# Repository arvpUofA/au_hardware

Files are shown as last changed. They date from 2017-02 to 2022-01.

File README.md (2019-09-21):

# au_hardware #

Welcome to ARVP's hardware design repository.

In here you can find all of our electrical designs.

### Github Guides
- http://rogerdudler.github.io/git-guide/ 
- Intro to GitHub with Hello World
- https://www.youtube.com/watch?v=0fKg7e37bQE 

## Branches
- master -  contains boards that have been fabricated, soldered, tested and are part of this year’s robot
- develop - contains boards that have been designed, approved, and the fab company has accepted their designs.
- project_branch - every new project is branched from develop. Naming convention of branch is as follows:

All names in lowercase and can only include alphanumeric characters and underscores.
The naming format will be `project_board` (e.g. `motor_breakout` or `power_main`)
If the project only contains one board (e.g. `killswitch`) then naming format will be `project`.
If this is a newer iteration of the same board create a branch with the version number `project_board_vx` (where `x` is the version number).

## Starting a new project

```
    # Clone the develop branch of the repository
    git clone -b develop https://github.com/arvpUofA/au_hardware 
    # Create a new branch from develop
    git checkout -b project_board   
    # Push the branch to remote
    git push -u origin project_board
```

Create folder structure for project as follows:
Inside the `au_hardware`/`project_board` branch, create the project folder if it does not exist. (e.g. `motor`, `power`, etc)
Inside the project folder create a board folder if it does not exist. If this is a different version of the same board, don’t create a new folder. Use the same folder as before. If the project contains only one board, you don’t need to create this folder.
Naming of the folder will follow the same conventions as branch naming conventions (no spaces please). 
Add required files to this folder. Make sure to commit and push periodically.

## Project requirements
Once the board design is complete, run the following:

- ERC on schematic - error checking for schematic
- DRC on board - design rule check for pcb. (e.g. drc/JLCPCB2Layer.drc file)
- Generate image files for schematic and pcb. Make sure the images are clear with at least 200dpi.
- Generate CAM files.
- Test CAM files using a CAM Viewer (e.g. View Mate or Gerbv)

Each project needs the following files:
- [ ] project_board.sch - schematic file for project
- [ ] project_board.brd - board file for project
- [ ] project_board_sch.png - image of schematic
- [ ] project_board_brd.png - image of pcb
- [ ] project_board/ - this folder contains all the CAM files
- [ ] project_board.zip - ZIP of the CAM folder

## Pull request and close

Once all requirements have been complete, create a pull request to merge this branch into develop

Set base: `develop` and compare: `your_branch`. Click "Create pull request".
 
Set the PR name, create a detailed description, and assign the team lead to review your pull request.   
The reviewer will check your design, and rerun ERC and DRC.

If the reviewer has any suggestions, implement them in your design, regenerate all required files and commit and push everything.

After the review is complete, the board will be uploaded to the fabrication website. If they approve the design, the reviewer will merge and close the pull request. Make sure you don’t continue work on this closed branch.
A new release tag will also be created for the board with format boardname[version]. E.g. killswitch1.0. At any point you can look at any older version by going to that specific tag.
Note that, if during reviews we discovered any changes we want to make in the next version, we will put these as issues on the repository and assign them to you. These need to be fixed in the next version before you make a PR.

## Starting a new revision

Once your PRs have been closed a.k.a the board has been sent out, the branch you were working on will be deleted, and you will need to make
a new branch off `develop` with the latest version number for that board.

```
    # To start switch to develop
    git checkout develop
    # Pull the latest version of the code
    git pull 
```

Create a new branch for the next iteration of the board. The naming format for the branch is `boardname_vx`

```
    # Example for V2 of comm_hub
    git checkout -b comm_hub_v2
```

Find the appropriate project folder where the current board revision is saved (e.g.  communications_hub) and create a new folder within this project folder with the new version number (e.g. communications_hub\communications_hub_v2).
Make sure to push your new branch to github using 

```
git push -u origin name_of_new_branch
```

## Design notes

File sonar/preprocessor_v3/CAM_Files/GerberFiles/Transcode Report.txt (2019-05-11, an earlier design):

   ---- Transcoding 'C:\Users\Andrew\Documents\Business\ARVP\au_hardware\sonar\preprocessor_v4\CAM_Files\GerberFiles\copper_inner_l2.gbr' ----   Wed Dec 26 16:14:29 2018

D10   --> D100
D12   --> D101
D13   --> D102
D14   --> D103
D15   --> D104
D16   --> D105
D17   --> D106
-----------------------------------------------------------------

   ---- Transcoding 'C:\Users\Andrew\Documents\Business\ARVP\au_hardware\sonar\preprocessor_v4\CAM_Files\GerberFiles\copper_inner_l3.gbr' ----   Wed Dec 26 16:14:29 2018

D10   --> D107
D12   --> D108
D13   --> D109
D14   --> D110
D15   --> D111
D16   --> D112
D17   --> D113
D18   --> D114
D19   --> D115
D20   --> D116
D21   --> D117
D22   --> D118
D23   --> D119
D24   --> D120
-----------------------------------------------------------------

   ---- Transcoding 'C:\Users\Andrew\Documents\Business\ARVP\au_hardware\sonar\preprocessor_v4\CAM_Files\GerberFiles\copper_top_l1.gbr' ----   Wed Dec 26 16:14:29 2018

D11   --> D121
D12   --> D122
D13   --> D123
D14   --> D124
D16   --> D125
D17   --> D126
D18   --> D127
D19   --> D128
D20   --> D129
D21   --> D130
D22   --> D131
D23   --> D132
D24   --> D133
D25   --> D134
D26   --> D135
D27   --> D136
D28   --> D137
D29   --> D138
-----------------------------------------------------------------

   ---- Transcoding 'C:\Users\Andrew\Documents\Business\ARVP\au_hardware\sonar\preprocessor_v4\CAM_Files\GerberFiles\profile.gbr' ----   Wed Dec 26 16:14:29 2018

D10   --> D139
-----------------------------------------------------------------

   ---- Transcoding 'C:\Users\Andrew\Documents\Business\ARVP\au_hardware\sonar\preprocessor_v4\CAM_Files\GerberFiles\silkscreen_bottom.gbr' ----   Wed Dec 26 16:14:29 2018

D10   --> D140
D11   --> D141
D12   --> D142
D13   --> D143
D14   --> D144
D15   --> D145
D16   --> D146
-----------------------------------------------------------------

   ---- Transcoding 'C:\Users\Andrew\Documents\Business\ARVP\au_hardware\sonar\preprocessor_v4\CAM_Files\GerberFiles\silkscreen_top.gbr' ----   Wed Dec 26 16:14:29 2018

D10   --> D147
D11   --> D148
D12   --> D149
D13   --> D150
D14   --> D151
D15   --> D152
D16   --> D153
D17   --> D154
D18   --> D155
D19   --> D156
D20   --> D157
D21   --> D158
D22   --> D159
D23   --> D160
D24   --> D161
D25   --> D162
-----------------------------------------------------------------

   ---- Transcoding 'C:\Users\Andrew\Documents\Business\ARVP\au_hardware\sonar\preprocessor_v4\CAM_Files\GerberFiles\soldermask_bottom.gbr' ----   Wed Dec 26 16:14:29 2018

D10   --> D163
D11   --> D164
D12   --> D165
D13   --> D166
D14   --> D167
D15   --> D168
D16   --> D169
D17   --> D170
D18   --> D171
D19   --> D172
D20   --> D173
-----------------------------------------------------------------

   ---- Transcoding 'C:\Users\Andrew\Documents\Business\ARVP\au_hardware\sonar\preprocessor_v4\CAM_Files\GerberFiles\soldermask_top.gbr' ----   Wed Dec 26 16:14:29 2018

D10   --> D174
D11   --> D175
D12   --> D176
D13   --> D177
D14   --> D178
D15   --> D179
D16   --> D180
D17   --> D181
D18   --> D182
D19   --> D183
D20   --> D184
D21   --> D185
D22   --> D186
D23   --> D187
D24   --> D188
D25   --> D189
D26   --> D190
D27   --> D191
D28   --> D192
D29   --> D193
D30   --> D194
D31   --> D195
D32   --> D196
D33   --> D197
D34   --> D198
D35   --> D199
D36   --> D200
D37   --> D201
D38   --> D202
D39   --> D203
D40   --> D204
D41   --> D205
D42   --> D206
D43   --> D207
D44   --> D208
D45   --> D209
D46   --> D210
D47   --> D211
D48   --> D212
D49   --> D213
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
-----------------------------------------------------------------

   ---- Transcoding 'C:\Users\Andrew\Documents\Business\ARVP\au_hardware\sonar\preprocessor_v4\CAM_Files\GerberFiles\solderpaste_bottom.gbr' ----   Wed Dec 26 16:14:29 2018

D10   --> D217
D11   --> D218
D12   --> D219
D13   --> D220
-----------------------------------------------------------------

   ---- Transcoding 'C:\Users\Andrew\Documents\Business\ARVP\au_hardware\sonar\preprocessor_v4\CAM_Files\GerberFiles\solderpaste_top.gbr' ----   Wed Dec 26 16:14:29 2018

D10   --> D221
D11   --> D222
D12   --> D223
D13   --> D224
D14   --> D225
D15   --> D226
D16   --> D227
D17   --> D228
D18   --> D229
D19   --> D230
D20   --> D231
D21   --> D232
D22   --> D233
D23   --> D234
D24   --> D235
D25   --> D236
D26   --> D237
D27   --> D238
D28   --> D239
D29   --> D240
D30   --> D241
D31   --> D242
D32   --> D243
D33   --> D244
D34   --> D245
D35   --> D246
D36   --> D247
D37   --> D248
D38   --> D249
D39   --> D250
D40   --> D251
D41   --> D252
D42   --> D253
D43   --> D254
-----------------------------------------------------------------

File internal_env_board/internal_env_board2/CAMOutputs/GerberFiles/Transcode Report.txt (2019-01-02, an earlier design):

   ---- Transcoding 'C:\Users\Andrew\Documents\Business\ARVP\au_hardware\internal_env_board\internal_env_board2\CAMOutputs\GerberFiles\copper_top.gbr' ----   Fri Dec 21 16:37:05 2018

D12   --> D100
D13   --> D101
D14   --> D102
D15   --> D103
D16   --> D104
D18   --> D105
D19   --> D106
D20   --> D107
D21   --> D108
D22   --> D109
D23   --> D110
-----------------------------------------------------------------

   ---- Transcoding 'C:\Users\Andrew\Documents\Business\ARVP\au_hardware\internal_env_board\internal_env_board2\CAMOutputs\GerberFiles\profile.gbr' ----   Fri Dec 21 16:37:05 2018

D10   --> D111
-----------------------------------------------------------------

   ---- Transcoding 'C:\Users\Andrew\Documents\Business\ARVP\au_hardware\internal_env_board\internal_env_board2\CAMOutputs\GerberFiles\silkscreen_bottom.gbr' ----   Fri Dec 21 16:37:05 2018

D10   --> D112
D11   --> D113
-----------------------------------------------------------------

   ---- Transcoding 'C:\Users\Andrew\Documents\Business\ARVP\au_hardware\internal_env_board\internal_env_board2\CAMOutputs\GerberFiles\silkscreen_top.gbr' ----   Fri Dec 21 16:37:06 2018

D10   --> D114
D11   --> D115
D12   --> D116
D13   --> D117
D14   --> D118
D15   --> D119
D16   --> D120
D17   --> D121
D18   --> D122
D19   --> D123
D20   --> D124
D21   --> D125
-----------------------------------------------------------------

   ---- Transcoding 'C:\Users\Andrew\Documents\Business\ARVP\au_hardware\internal_env_board\internal_env_board2\CAMOutputs\GerberFiles\soldermask_bottom.gbr' ----   Fri Dec 21 16:37:06 2018

D10   --> D126
D11   --> D127
D12   --> D128
D13   --> D129
D14   --> D130
D15   --> D131
D16   --> D132
D17   --> D133
D18   --> D134
-----------------------------------------------------------------

   ---- Transcoding 'C:\Users\Andrew\Documents\Business\ARVP\au_hardware\internal_env_board\internal_env_board2\CAMOutputs\GerberFiles\soldermask_top.gbr' ----   Fri Dec 21 16:37:06 2018

D10   --> D135
D11   --> D136
D12   --> D137
D13   --> D138
D14   --> D139
D15   --> D140
D16   --> D141
D17   --> D142
D18   --> D143
D19   --> D144
D20   --> D145
D21   --> D146
D22   --> D147
D23   --> D148
D24   --> D149
D25   --> D150
D26   --> D151
D27   --> D152
D28   --> D153
D29   --> D154
D30   --> D155
-----------------------------------------------------------------

   ---- Transcoding 'C:\Users\Andrew\Documents\Business\ARVP\au_hardware\internal_env_board\internal_env_board2\CAMOutputs\GerberFiles\solderpaste_bottom.gbr' ----   Fri Dec 21 16:37:06 2018

D10   --> D156
D11   --> D157
-----------------------------------------------------------------

   ---- Transcoding 'C:\Users\Andrew\Documents\Business\ARVP\au_hardware\internal_env_board\internal_env_board2\CAMOutputs\GerberFiles\solderpaste_top.gbr' ----   Fri Dec 21 16:37:06 2018

D10   --> D158
D11   --> D159
D12   --> D160
D13   --> D161
D14   --> D162
D15   --> D163
D16   --> D164
D17   --> D165
D18   --> D166
D19   --> D167
D20   --> D168
D21   --> D169
D22   --> D170
D23   --> D171
-----------------------------------------------------------------

   ---- Transcoding 'C:\Users\Andrew\Documents\Business\ARVP\au_hardware\internal_env_board\internal_env_board2\CAMOutputs\GerberFiles\copper_top.gbr' ----   Fri Dec 21 16:52:00 2018

D12   --> D100
D13   --> D101
D14   --> D102
D15   --> D103
D16   --> D104
D18   --> D105
D19   --> D106
D20   --> D107
D21   --> D108
D22   --> D109
D23   --> D110
-----------------------------------------------------------------

   ---- Transcoding 'C:\Users\Andrew\Documents\Business\ARVP\au_hardware\internal_env_board\internal_env_board2\CAMOutputs\GerberFiles\profile.gbr' ----   Fri Dec 21 16:52:00 2018

D10   --> D111
-----------------------------------------------------------------

   ---- Transcoding 'C:\Users\Andrew\Documents\Business\ARVP\au_hardware\internal_env_board\internal_env_board2\CAMOutputs\GerberFiles\silkscreen_bottom.gbr' ----   Fri Dec 21 16:52:00 2018

D10   --> D112
D11   --> D113
-----------------------------------------------------------------

   ---- Transcoding 'C:\Users\Andrew\Documents\Business\ARVP\au_hardware\internal_env_board\internal_env_board2\CAMOutputs\GerberFiles\silkscreen_top.gbr' ----   Fri Dec 21 16:52:00 2018

D10   --> D114
D11   --> D115
D12   --> D116
D13   --> D117
D14   --> D118
D15   --> D119
D16   --> D120
D17   --> D121
D18   --> D122
D19   --> D123
D20   --> D124
D21   --> D125
-----------------------------------------------------------------

   ---- Transcoding 'C:\Users\Andrew\Documents\Business\ARVP\au_hardware\internal_env_board\internal_env_board2\CAMOutputs\GerberFiles\soldermask_bottom.gbr' ----   Fri Dec 21 16:52:00 2018

D10   --> D126
D11   --> D127
D12   --> D128
D13   --> D129
D14   --> D130
D15   --> D131
D16   --> D132
D17   --> D133
D18   --> D134
-----------------------------------------------------------------

   ---- Transcoding 'C:\Users\Andrew\Documents\Business\ARVP\au_hardware\internal_env_board\internal_env_board2\CAMOutputs\GerberFiles\soldermask_top.gbr' ----   Fri Dec 21 16:52:00 2018

D10   --> D135
D11   --> D136
D12   --> D137
D13   --> D138
D14   --> D139
D15   --> D140
D16   --> D141
D17   --> D142
D18   --> D143
D19   --> D144
D20   --> D145
D21   --> D146
D22   --> D147
D23   --> D148
D24   --> D149
D25   --> D150
D26   --> D151
D27   --> D152
D28   --> D153
D29   --> D154
D30   --> D155
-----------------------------------------------------------------

   ---- Transcoding 'C:\Users\Andrew\Documents\Business\ARVP\au_hardware\internal_env_board\internal_env_board2\CAMOutputs\GerberFiles\solderpaste_bottom.gbr' ----   Fri Dec 21 16:52:00 2018

D10   --> D156
D11   --> D157
-----------------------------------------------------------------

   ---- Transcoding 'C:\Users\Andrew\Documents\Business\ARVP\au_hardware\internal_env_board\internal_env_board2\CAMOutputs\GerberFiles\solderpaste_top.gbr' ----   Fri Dec 21 16:52:00 2018

D10   --> D158
D11   --> D159
D12   --> D160
D13   --> D161
D14   --> D162
D15   --> D163
D16   --> D164
D17   --> D165
D18   --> D166
D19   --> D167
D20   --> D168
D21   --> D169
D22   --> D170
D23   --> D171
-----------------------------------------------------------------

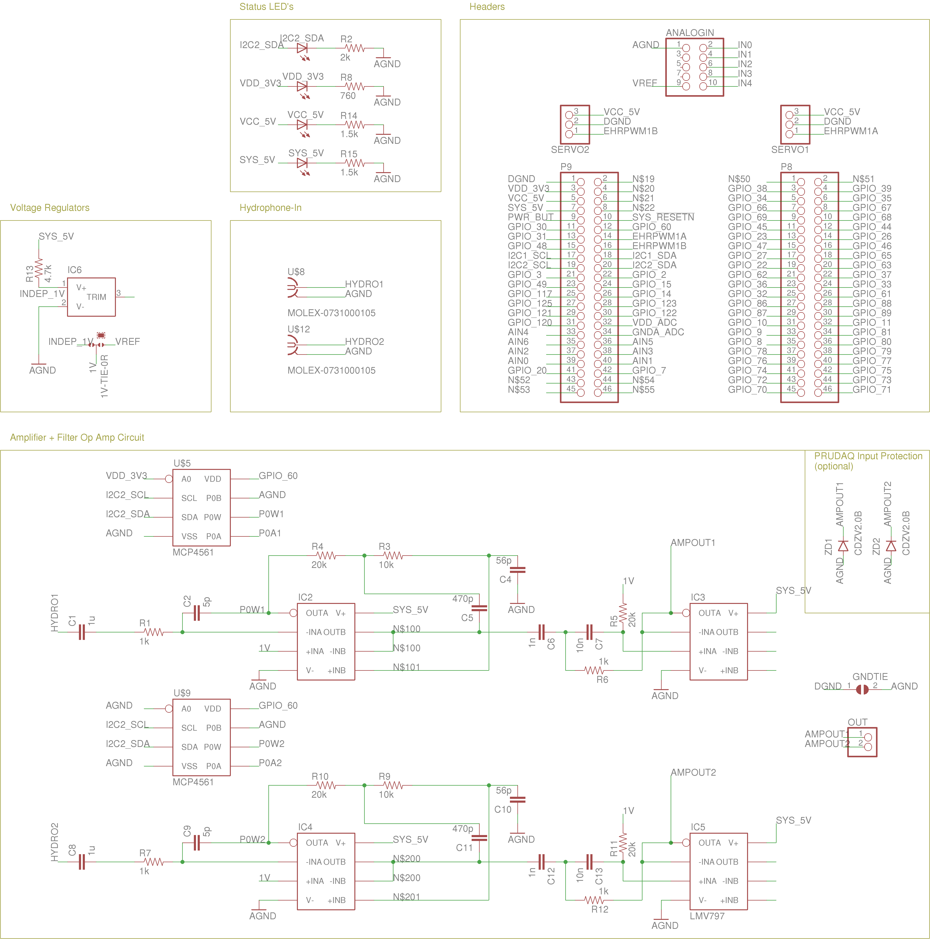
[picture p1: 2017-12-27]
sonar/amp/sonar_amp_sch.png

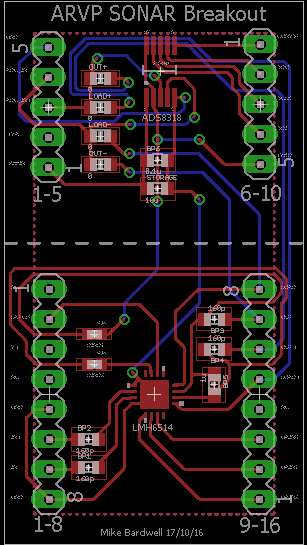
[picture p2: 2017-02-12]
sonar/ampandadc/sonar_ampandadc_brd.png

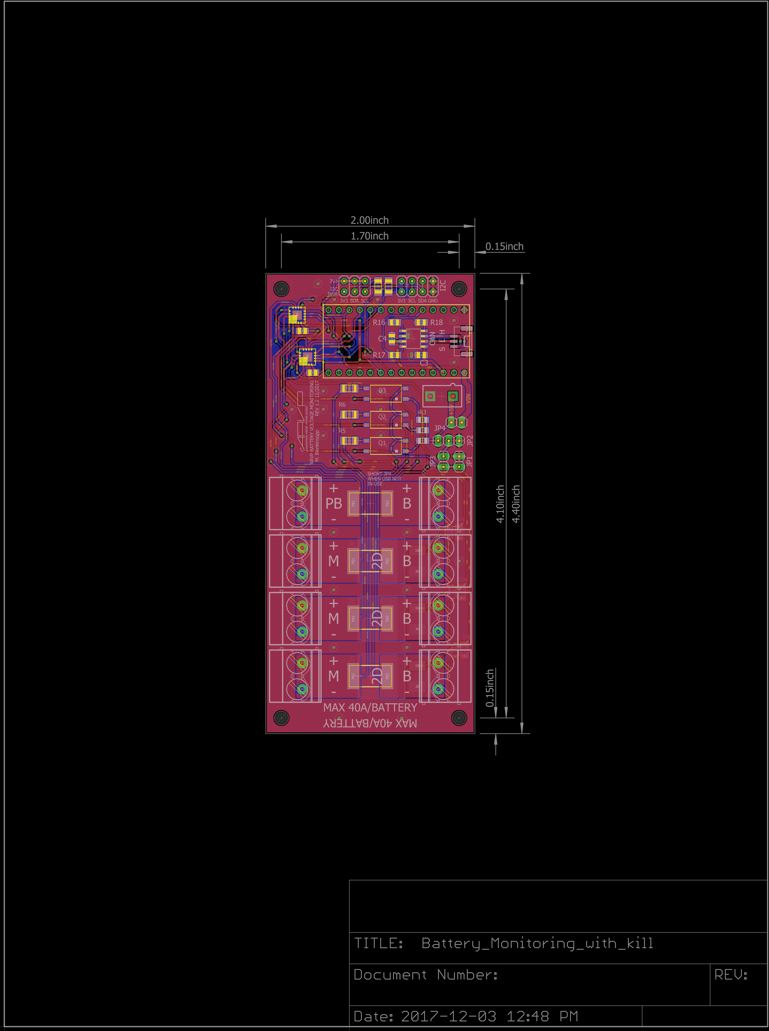
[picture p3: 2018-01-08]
battery_monitoring_board/V1_2017_2018/Battery_Monitoring_with_kill_pcb.png

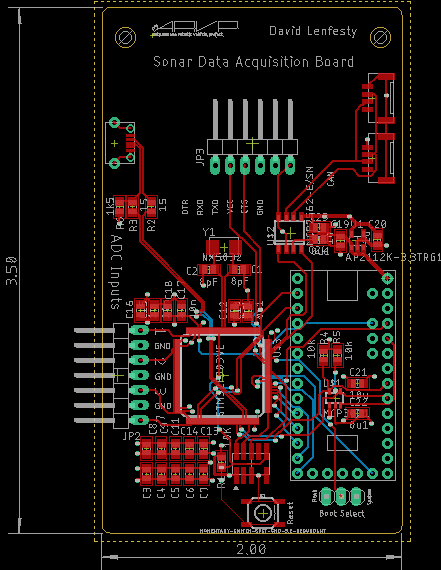
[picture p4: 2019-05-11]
sonar/integrated_adc/integrated_adc_board.png

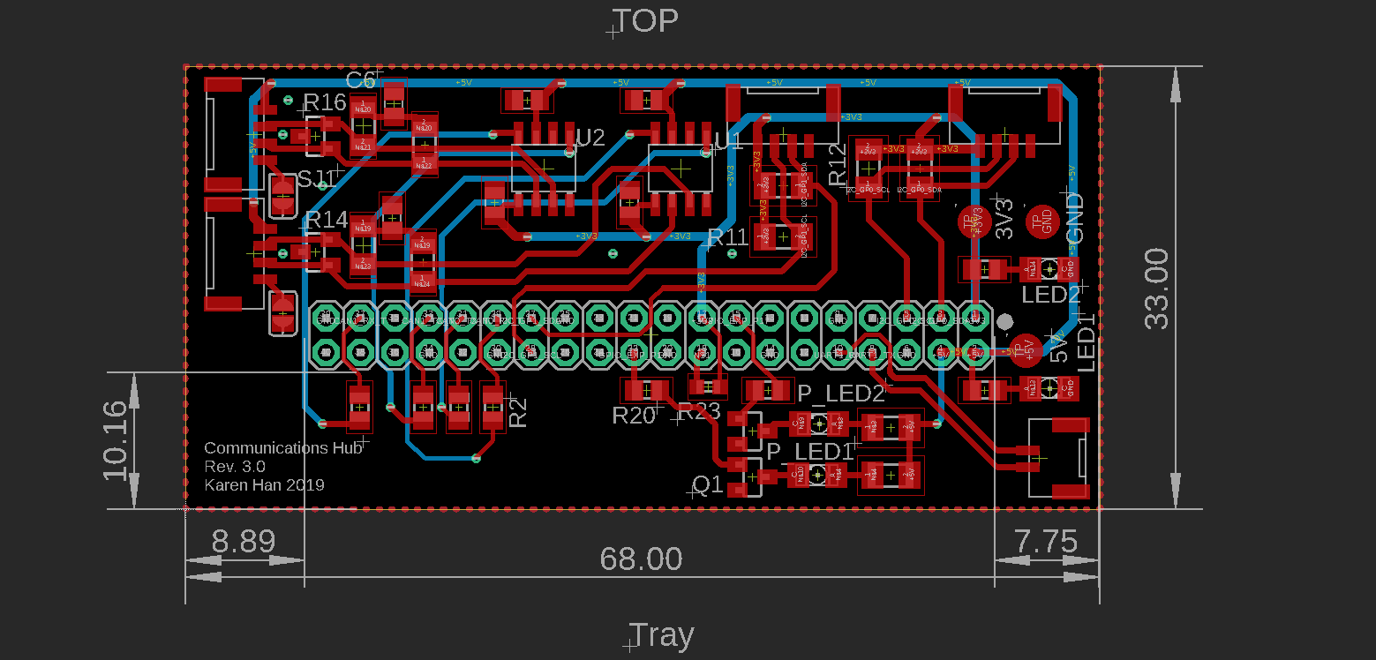
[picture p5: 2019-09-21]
communications_hub/com_hub_brd.PNG

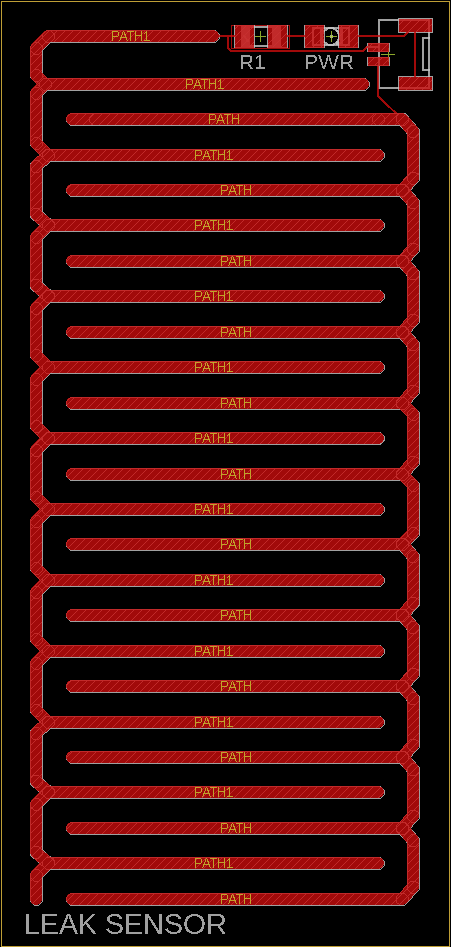
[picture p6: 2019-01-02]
leak_sensor/LeakSensor_brd.png

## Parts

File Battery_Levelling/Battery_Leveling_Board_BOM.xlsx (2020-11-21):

Shematic Reference Number | Part Description | Manufacturer Part Number | Datasheet | Price | Quantity Required | On hand | Quantity To Buy | Total Cost | Customer Reference
R1,3 | RES SMD 220 OHM 1% 1/8W 0805 | RC0805FR-07220RL | http://www.yageo.com/documents/recent/PYu-RC_Group_51_RoHS_L_7.pdf | 0.031 | 2 |  |  | 0.062
R9,10 | RES SMD 1K OHM 1% 1/8W 0805 | RC0805FR-071KL | http://www.yageo.com/documents/recent/PYu-RC_Group_51_RoHS_L_7.pdf | 0.034 | 1 |  |  | 0.034
C5,6 | CAP CER 10UF 16V X7R 0805 | CL21B106KOQNNNG | http://www.samsungsem.com/kr/support/product-search/mlcc/CL21B106KOQNNNG.jsp | 0.39 | 2 |  |  | 0.78
U7 | IC TRANSCEIVER HALF 1/1 8SOIC | MCP2562-E/SN | http://ww1.microchip.com/downloads/en/DeviceDoc/20005167C.pdf | 1.28 | 1 |  |  | 2.05
CON1 | CONN HEADER 2POS 4.2MM VERT TIN | 39281023 | http://www.molex.com/pdm_docs/sd/039281023_sd.pdf | 0.83 | 1 |  |  | 0.83
JP6 | CONN HEADER VERT 2POS | M20-9990245 | https://cdn.harwin.com/pdfs/M20-999.pdf | 0.2 | 2 |  |  | 0.4
Teensy | CONN HEADER FMALE 14POS .1" GOLD | PPPC141LFBN-RC | http://www.sullinscorp.com/drawings/78_P(N)PxCxxxLFBN-RC,_10492-H.pdf | 1.28 | 2 |  |  | 2.56
5V | LED GREEN CLEAR 1206 SMD | LTST-C150GKT | http://optoelectronics.liteon.com/upload/download/DS-22-98-0004/LTST-C150GKT.pdf | 0.46 | 2 |  |  | 0.92
DANGER | LED RED CLEAR 1206 SMD | LTST-C150EKT | https://media.digikey.com/pdf/Data%20Sheets/Lite-On%20PDFs/LTST-C150EKT.pdf | 0.5 | 1 |  |  | 0.5
R2,8 | RES SMD 240 OHM 1% 1/4W 1206 | RC1206FR-07240RL | http://www.yageo.com/documents/recent/PYu-RC_Group_51_RoHS_L_7.pdf | 0.047 | 2 |  |  | 0.094
CON2,3 | CONN HEADER GH SIDE 3POS 1.25MM | SM03B-GHS-TB(LF)(SN) | http://www.jst-mfg.com/product/pdf/eng/eGH.pdf | 0.68 | 2 |  |  | 1.36
U2-5 | IC OR CTRLR N+1 6SOT | LM5050MK-2/NOPB | http://www.ti.com/lit/ds/symlink/lm5050-2.pdf | 3.56 | 4 |  |  | 14.24
C1-4 | CAP CER SMD 0805 .01UF X7R 5% 50 | C0805C103J5RAC7210 | https://content.kemet.com/datasheets/KEM_C1002_X7R_SMD.pdf | 0.16 | 4 |  |  | 0.64
Q1-4 | MOSFET N-CH 30V 90A TO252 | SUD50N03-06AP-E3 | http://www.vishay.com/docs/73540/73540.pdf | 2.18 | 4 |  |  | 8.72
R5-7,11 | RES SMD 100K OHM 1% 1/4W 1206 | 311-100KFRCT-ND | https://www.yageo.com/upload/media/product/productsearch/datasheet/rchip/PYu-RC_Group_51_RoHS_L_10.pdf | 0.15 | 4 |  |  | 0.6
J1-6 | TERM BLK 2P SIDE ENT 6.35MM PCB | 1714955 | https://media.digikey.com/pdf/Data%20Sheets/Phoenix%20Contact%20PDFs/1714955.pdf | 2.46 | 6 |  |  | 14.76
U6 | IC GATE DRVR HI/LOW SIDE 8SOIC | IR2301SPBF‎ | http://ww1.microchip.com/downloads/en/DeviceDoc/20005167C.pdf | 2.71 | 1 |  |  | 2.71
R4 | RES SMD 5.1 OHM 5% 1/4W 1206 | ‎RC1206JR-075R1L‎ | https://www.yageo.com/upload/media/product/productsearch/datasheet/rchip/PYu-RC_Group_51_RoHS_L_10.pdf | 0.18 | 1 |  |  | 0.18
C8 | CAP CER 10UF 50V X5R 1206 | CL31A106MBHNNNE‎ | http://www.samsungsem.com/kr/support/product-search/mlcc/CL31A106MBHNNNE.jsp | 0.47 | 1 |  |  | 0.47
C7 | CAP CER 1.5UF 50V JB 0805 | C2012JB1H155M125AB‎ | https://product.tdk.com/info/en/catalog/datasheets/mlcc_commercial_general_en.pdf?ref_disty=digikey | 0.76 | 1 |  |  | 0.76
D1 | DIODE SCHOTTKY 40V 1A DO214AC | ‎CDBA140-G‎ | http://www.comchiptech.com/admin/files/product/CDBA140-HF%20Thru192841.%20CDBA1100-HF%20RevB.pdf | 0.49 | 1 |  |  | 0.49
Q5 | MOSFET N-CH 20V 21A 8-TSSOP | DMN2011UTS-13 | https://www.diodes.com/assets/Datasheets/DMN2011UTS.pdf | 0.79 | 1 |  |  | 0.79

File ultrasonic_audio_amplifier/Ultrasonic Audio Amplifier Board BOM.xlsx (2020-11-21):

Shematic Reference Number | Part Description | Digikey Part Number | Manufacturer Part Number | Datasheet | Price | Quantity Required | On hand | Quantity To Buy | Total Cost | Customer Reference
Capacitors |  |  |  |  |  |  |  |  |  | Cart Share
C1 | CAP FILM 220PF 5% 400VDC RAD | 1928-1267-ND | FKP2G002201D00JSSD | https://www.wima.de/wp-content/uploads/media/e_WIMA_FKP_2.pdf | $0.64 | 1 |  | 1 | $0.64 | https://www.digikey.ca/short/zbdm1r
C2 | CAP FILM 150PF 5% 250VDC RAD | 1928-1251-ND | FKP2F001501D00JSC9 | https://www.wima.de/wp-content/uploads/media/e_WIMA_FKP_2.pdf | $0.61 | 1 |  | 1 | $0.61
C3 | CAP CER 4.7UF 10% 25V X5R 0805 | 490-12753-2-ND | GRM219R61E475KA73D | https://search.murata.co.jp/Ceramy/image/img/A01X/G101/ENG/GRM219R61E475KA73-01.pdf | $0.44 | 1 |  | 1 | $0.44
C4, C6 | CAP CER 0.1UF 50V X7R 0805 | 1276-1003-2-ND | CL21B104KBCNNNC | https://media.digikey.com/pdf/Data%20Sheets/Samsung%20PDFs/CL21B104KBCNNN_Spec.pdf | $0.15 | 2 |  | 2 | $0.30
C5 | CAP CER 24PF 50V C0G/NP0 0805 | 1276-2619-1-ND‎ | ‎CL21C240JBANNNC‎ | https://www.digikey.ca/product-detail/en/CL21C240JBANNNC/1276-2619-1-ND/3890705/?itemSeq=330570145 | $0.15 | 1 |  | 1 | $0.15
C7 | CAP CER 10UF 25V X5R 1206 | 1276-1181-2-ND | CL31A106MAHNNNE | http://www.samsungsem.com/kr/support/product-search/mlcc/CL31A106MAHNNNE.jsp | $0.30 | 1 |  | 1 | $0.30
C8 | CAP CER 1UF 25V X7R 1206 | 1276-3086-2-ND | CL31B105KAHNFNE | http://www.samsungsem.com/kr/support/product-search/mlcc/CL31B105KAHNFNE.jsp | $0.24 | 1 |  | 1 | $0.24
Resistors
R1, R2 | RES 1K OHM 1% 1/4W 1206 | RMCF1206FT1K00TR-ND | RMCF1206FT1K00 | https://www.seielect.com/catalog/sei-rmcf_rmcp.pdf | $0.16 | 1 |  | 1 | $0.16
R3, R4, R7 | RES SMD 10K OHM 1% 1/8W 0805 | 311-10.0KCRTR-ND | RC0805FR-0710KL | https://www.yageo.com/upload/media/product/productsearch/datasheet/rchip/PYu-RC_Group_51_RoHS_L_10.pdf | $0.16 | 3 |  | 3 | $0.48
R5 | RES 2.7 OHM 1% 1/4W 1206 | 2019-RK73H2BTTD2R70FTR-ND | RK73H2BTTD2R70F | http://www.koaspeer.com/pdfs/RK73H.pdf | $0.16 | 1 |  | 1 | $0.16
R6 | RES 1M OHM 1% 1/8W 0805 | 541-4135-2-ND | CRCW08051M00FKEAC | http://www.vishay.com/docs/28773/crcwce3.pdf | $0.16 | 1 |  | 1 | $0.16
Connectors
CON1 (5V) | CONN HEADER VERT 2POS | WM3800-ND | 39281023 | https://www.molex.com/pdm_docs/sd/039281023_sd.pdf | $0.80 | 1 |  | 1 | $0.80
J1, J2 | TERM BLK 2P SIDE ENT 2.54MM PCB | A98333-ND | 282834-2 | https://www.te.com/commerce/DocumentDelivery/DDEController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 | $1.85 | 2 |  | 2 | $3.70
J3 | TERM BLK 2P SIDE ENT 6.35MM PCB | ED2675-ND | OSTT7020150 | https://media.digikey.com/pdf/Data%20Sheets/On%20Shore%20PDFs/OSTT7xx0150.pdf | $1.48 | 1 |  | 1 | $1.48
JP1 | MACHINE PIN SOCKET 4P 1.00MM PIT | 2057-SMC-1-04-1-GT-ND | SMC-1-04-1-GT | http://www.adam-tech.com/downloader.php?p=SMC-1-XX-1-GT.pdf | $0.33 | 1 |  | 1 | $0.33
SW1 | SWITCH SLIDE DIP SPST 100MA 20V | CT2102MS-ND | 210-2MS | https://www.ctscorp.com/wp-content/uploads/209-210.pdf | $0.66 | 1 |  | 1 | $0.66
Others
U1 | IC DGTL POT 45KOHM 64TAP 16SO | DS1881Z-050+-ND | DS1881Z-050+ | https://datasheets.maximintegrated.com/en/ds/DS1881.pdf | $3.21 | 1 |  | 1 | $3.21
U2 | IC AMP CLASS AB MONO 5.5W 14DIP | LM384N/NOPB-ND | LM384N/NOPB | http://www.ti.com/general/docs/suppproductinfo.tsp?distId=10 | $3.07 | 1 |  | 1 | $3.07
Heatsink | HEATSINK CPU FORGED | AE11381-ND | V2032B | http://www.assmann-wsw.com/fileadmin/datasheets/ASS_0815_HS.pdf | $3.81 | 1 |  | 1 | $3.81
Thermal pad | THERM PAD 19.05MMX12.7MM GRAY | 3M12137-ND | 5590H-TO220 | https://multimedia.3m.com/mws/media/920112O/3mtm-thermally-conductive-acrylic-interface-pad-5590h.pdf | $1.27 | 1 |  | 1 | $1.27 | Total | 21.97

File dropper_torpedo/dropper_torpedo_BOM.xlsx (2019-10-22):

Torpedo Board V3: Bill of Materials
Shematic Reference Number | Part Description | Manufacturer Part Number | Datasheet | Price | Quantity | Total Cost | Customer Reference
Q1, Q2 | MOSFET N-CH 80V 6.7A 8-SOIC | SI4896DY-T1-E3 | http://www.vishay.com/docs/71300/71300.pdf | 2.37 | 2 | 4.74 | DROP_TORP
Q3, Q4 | MOSFET 2N-CH 30V 8.1A 8SOIC | IRL6372TRPBF | http://www.infineon.com/dgdl/irl6372pbf.pdf?fileId=5546d462533600a401535660046e2579 | 1.15 | 2 | 2.3 | DROP_TORP
D1, D2 | DIODE SCHOTTKY 30V 1A SMA | STPS1L30A | http://www.st.com/content/ccc/resource/technical/document/datasheet/d4/83/f4/ff/dc/cc/48/7f/CD00001323.pdf/files/CD00001323.pdf/jcr:content/translations/en.CD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 | 0.53 | 2 | 1.06 | DROP_TORP
U1, U2 | OPTOISO 3.75KV DARLINGTON 4SOP | LTV-355T | http://optoelectronics.liteon.com/upload/download/DS70-2001-006/LTV-355T%20series%20201610.pdf | 0.74 | 2 | 1.48 | DROP_TORP
TRM1, TRM2 | TERM BLOCK 5.08MM HORZ 2POS PCB | OSTTC022162 | http://www.on-shore.com/wp-content/uploads/2015/09/osttcxx2162.pdf | 1.08 | 2 | 2.16 | DROP_TORP
LED1-5 | LED GREEN CLEAR 1206 SMD | LTST-C150GKT | http://optoelectronics.liteon.com/upload/download/DS-22-98-0004/LTST-C150GKT.pdf | 0.46 | 2 | 0.92 | DROP_TORP
X2 | CONN HEADER 4POS 4.2MM VERT TIN | 39281043 | http://www.molex.com/pdm_docs/sd/039281043_sd.pdf | 1.04 | 1 | 1.04 | DROP_TORP
R14-17 | RES ARRAY 4 RES 220 OHM 1206 | EXB-V8V221JV | https://media.digikey.com/pdf/Data%20Sheets/Panasonic%20Resistors%20Thermistors%20PDFs/EXBV8V%20Spec.pdf | 0.14 | 4 | 0.56 | DROP_TORP
R22,26 | RES ARRAY 4 RES 10K OHM 1206 | EXB-V8V103JV | https://media.digikey.com/pdf/Data%20Sheets/Panasonic%20Resistors%20Thermistors%20PDFs/EXBV8V%20Spec.pdf | 0.14 | 2 | 0.28 | DROP_TORP
X1 | CONN TERM BLOCK 2.54MM 5POS PCB | OSTVN05A150 | http://www.on-shore.com/wp-content/uploads/2015/09/ostvnxxa150.pdf | 2.34 | 1 | 2.34 | DROP_TORP
C1,2 | CAP CER 1UF 50V X7R 1206 | CL31B105KBHNNNE | https://www.samsungsem.com/kr/support/product-search/mlcc/__icsFiles/afieldfile/2016/08/18/S_CL31B105KBHNNNE.pdf | 0.26 | 2 | 0.52 | DROP_TORP
C3,4,5 | CAP CER 10UF 16V X7R 0805 | CL21B106KOQNNNG | http://www.samsungsem.com/kr/support/product-search/mlcc/CL21B106KOQNNNG.jsp | 0.39 | 3 | 1.17 | DROP_TORP
R23 | RES SMD 240 OHM 1% 1/4W 1206 | RC1206FR-07240RL | http://www.yageo.com/documents/recent/PYu-RC_Group_51_RoHS_L_7.pdf | 0.047 | 1 | 0.047 | DROP_TORP
R24 | RES SMD 576 OHM 1% 1/4W 1206 | RC1206FR-07576RL | http://www.yageo.com/documents/recent/PYu-RC_Group_51_RoHS_L_7.pdf | 0.047 | 1 | 0.047 | DROP_TORP
R5,6 | RES SMD 1K OHM 1% 1/4W 1206 | RC1206FR-071KL | http://www.yageo.com/documents/recent/PYu-RC_Group_51_RoHS_L_7.pdf | 0.047 | 2 | 0.094 | DROP_TORP
R7,8,25 | RES SMD 2K OHM 1% 1/4W 1206 | RC1206FR-072KL | http://www.yageo.com/documents/recent/PYu-RC_Group_51_RoHS_L_7.pdf | 0.047 | 3 | 0.141 | DROP_TORP
R9-12 | RES SMD 4.99K OHM 1% 1/4W 0805 | RC0805FR-074K99L | http://www.yageo.com/documents/recent/PYu-RC_Group_51_RoHS_L_8.pdf | 0.031 | 4 | 0.124 | DROP_TORP
R18, 19 | RES SMD 220 OHM 1% 1/8W 0805 | RC0805FR-07220RL | http://www.yageo.com/documents/recent/PYu-RC_Group_51_RoHS_L_7.pdf | 0.031 | 2 | 0.062 | DROP_TORP
R1,2 | RES SMD 3K OHM 1% 1/4W 1206 | RC1206FR-073KL | http://www.yageo.com/documents/recent/PYu-RC_Group_51_RoHS_L_7.pdf | 0.047 | 2 | 0.094 | DROP_TORP
R3,4,20,21 | RES SMD 10K OHM 1% 1/4W 1206 | RC1206FR-0710KL | http://www.yageo.com/documents/recent/PYu-RC_Group_51_RoHS_L_7.pdf | 0.047 | 4 | 0.188 | DROP_TORP
R13 | RES SMD 1K OHM 1% 1/8W 0805 | RC0805FR-071KL | http://www.yageo.com/documents/recent/PYu-RC_Group_51_RoHS_L_7.pdf | 0.034 | 1 | 0.034 | DROP_TORP
U4 | IC LED DRIVER RGBA 28-TSSOP | PCA9685PW,118 | http://www.nxp.com/documents/data_sheet/PCA9685.pdf | 3.3 | 1 | 3.3 | DROP_TORP
Teensy 3.2 | CONN HEADER FMALE 14POS .1" GOLD | PPPC141LFBN-RC | http://www.sullinscorp.com/drawings/78_P(N)PxCxxxLFBN-RC,_10492-H.pdf | 1.28 | 2 | 2.56 | DROP_TORP
JP1-7,9,10 | DIL VERTICAL PC TAIL PIN HEADER 2x3 | M20-9980345 | https://cdn.harwin.com/pdfs/M20-998.pdf | 0.348 | 9 | 3.132 | DROP_TORP
JP8 | DIL VERTICAL PC TAIL PIN HEADER 2x4 | M20-9980445 | https://cdn.harwin.com/pdfs/M20-998.pdf | 0.48 | 1 | 0.48 | DROP_TORP
JP11 | SIL VERTICAL PC TAIL PIN HEADER 1x2 | M20-9990245 | https://cdn.harwin.com/pdfs/M20-999.pdf | 0.2 | 1 | 0.2 | DROP_TORP
U3 | IC TXRX CAN FAULT PROT 8SOIC | TCAN1042HVDRQ1 | http://www.ti.com/lit/ds/symlink/tcan1042hgv-q1.pdf | 2.05 | 1 | 2.05 | DROP_TORP
CON3 | CONN HEADER 2POS 4.2MM VERT TIN | 39281023 | http://www.molex.com/pdm_docs/sd/039281023_sd.pdf | 0.83 | 1 | 0.83 | DROP_TORP
CON1,2 | CONN HEADER GH SIDE 3POS 1.25MM | SM03B-GHS-TB(LF)(SN) | http://www.jst-mfg.com/product/pdf/eng/eGH.pdf | 0.68 | 2 | 1.36 | DROP_TORP
- | CONN JUMPER SHORTING GOLD FLASH | SPC02SYAN | http://www.sullinscorp.com/drawings/134_C02SYAN_11134.pdf | 0.083 | 9 | 0.747 | DROP_TORP
 |  |  |  |  | Total | 34.06

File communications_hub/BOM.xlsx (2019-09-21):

Shematic Reference Number | Part Description | Manufacturer Part Number | Datasheet | Price | Quantity | Total Cost | Customer Reference | Column1
R9 R10 R11 R12 R8 R7 | RES SMD 10K OHM 1% 1/8W 0805 | RC0805FR-0710KL | http://www.yageo.com/documents/recent/PYu-RC_Group_51_RoHS_L_7.pdf | $0.05 | 4 | $0.19 | COM_HUB | R7/R8 removed
R20 R1 R2 R19 R4 R5 | RES SMD 220 OHM 1% 1/8W 0805 | RC0805FR-07220RL | http://www.yageo.com/documents/recent/PYu-RC_Group_51_RoHS_L_7.pdf | $0.03 | 6 | $0.19 | COM_HUB
R6 R3 | RES SMD 1K OHM 1% 1/8W 0805 | RC0805FR-071KL | http://www.yageo.com/documents/recent/PYu-RC_Group_51_RoHS_L_7.pdf | $0.03 | 0 | $0.00 | COM_HUB | removed
C5 6 | CAP CER 4700PF 50V X7R 0805 | C0805X472K5RACAUTO | https://www.digikey.ca/product-detail/en/kemet/C0805X472K5RACAUTO/399-19471-6-ND/9742374 | $0.55 | 2 | $1.10 | COM_HUB
C1 2 3 4 | CAP CER 0.1UF 50V Y5V 0805 | CL21F104ZBCNNNC | http://www.samsungsem.com/kr/support/product-search/mlcc/CL21F104ZBCNNNC.jsp | $0.15 | 4 | $0.60 | COM_HUB
 | IC TXRX CAN 8SOIC | MCP2562-E/SN | http://ww1.microchip.com/downloads/en/DeviceDoc/20005284A.pdf | $1.42 | 2 | $2.84 | COM_HUB
 | CONN HEADER 2POS 4.2MM VERT TIN | 39281023 | http://www.molex.com/pdm_docs/sd/039281023_sd.pdf | $0.83 | 1 | $0.83 | COM_HUB
 | SIL VERTICAL PC TAIL PIN HEADER 1x2 | M20-9990245 | https://cdn.harwin.com/pdfs/M20-999.pdf | $0.20 | 1 | $0.20 | COM_HUB
Q1 Q2 | MOSFET N-CH 50V 300MA SOT23-3 | DMN5L06K-7 | https://www.digikey.ca/product-detail/en/diodes-incorporated/DMN5L06K-7/DMN5L06KDITR-ND/1287185 | $0.57 | 2 | $1.14 | COM_HUB
 | LED RED CLEAR 640NM SMD | XZM2MR55W-3 | https://www.digikey.ca/product-detail/en/sunled/XZM2MR55W-3/1497-1364-2-ND/6709133 | $0.62 | 3 | $1.86 | COM_HUB
 | LED YELLOW CLEAR 1206 SMD | XZMYK55W-3 | https://www.digikey.ca/product-detail/en/sunled/XZMYK55W-3/1497-1196-1-ND/4745902 | $0.50 | 1 | $0.50 | COM_HUB
 | CONN RCPT 40POS 0.1 TIN PCB | SSQ-120-03-T-D-005-ND | https://www.digikey.ca/product-detail/en/samtec-inc/SSQ-120-03-T-D-005/SSQ-120-03-T-D-005-ND/8094930 | $5.99 | 1 | $5.99 | COM_HUB
R17 16 15 14 | RES SMD 62 OHM 1% 1/4W 1206 | 311-62ERCT-ND | https://www.digikey.ca/product-detail/en/samsung-electro-mechanics/RC3216F121CS/1276-5672-1-ND/3968644 | $0.15 | 4 | $0.60 | COM_HUB
 | CONN HEADER GH SIDE 4POS 1.25MM | SM04B-GHS-TB(LF)(SN)- | https://www.digikey.ca/product-detail/en/jst-sales-america-inc/SM04B-GHS-TB-LF-SN/455-1566-1-ND/807834 | $0.45 | 4 | $1.80 | COM_HUB
 | CONN HEADER GH SIDE 2POS 1.25MM | SM02B-GHS-TB(LF)(SN) | https://www.digikey.ca/product-detail/en/jst-sales-america-inc/SM02B-GHS-TB-LF-SN/455-1564-1-ND/807832 | $0.46 | 1 | $0.46 | COM_HUB
R22 R18? | RES SMD 68 OHM 1% 1/8W 0805 | RC0805FR-0768RL | http://www.yageo.com/documents/recent/PYu-RC_Group_51_RoHS_L_9.pdf | $0.15 | 2 | $0.30 | COM_HUB
R23 | RES SMD 4.7K OHM 5% 1/10W 0603 | RC0603JR-074K7L | http://www.yageo.com/documents/recent/PYu-RC_Group_51_RoHS_L_10.pdf | $0.15 | 1 | $0.15 | COM_HUB
R13 R21 | RES SMD 140 OHM 1% 1/8W 0805 | RC0805FR-07140RL | http://www.yageo.com/documents/recent/PYu-RC_Group_51_RoHS_L_9.pdf | $0.15 | 2 | $0.30 | COM_HUB
U4 U5 | TVS DIODE 24V 44V SOT23-3 | NUP2105LT1G | http://www.onsemi.com/pub/Collateral/NUP2105L-D.PDF | $0.68 | 2 |  | COM_HUB
 |  |  |  |  | Total | $19.04

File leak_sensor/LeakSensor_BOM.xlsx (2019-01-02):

Schematic Reference Number | Part Description | Manufacturer Part Number | Datasheet | Price | Quantity | Total
CON4-1, CON4-2, CON4-TABS | CONN HEADER GH SIDE 2POS 1.25MM | SM02B-GHS-TB(LF)(SN) | Link (http://www.jst-mfg.com/product/pdf/eng/eGH.pdf) | $0.65 | 1 | $0.65
PWR | LED RED CLEAR 1206 SMD | LTST-C150CKT | Link (http://optoelectronics.liteon.com/upload/download/DS-22-98-0002/LTST-C150CKT.pdf) | $0.52 | 1 | $0.52
R1 | RES SMD 37.4 OHM 1% 1/4W 1206 | RC1206FR-0737R4L | Link (https://www.digikey.ca/en/datasheets/yageo/yageo-pyu-r_marking_2) | $0.15 | 1 | $0.15
Total |  |  |  |  |  | $1.32

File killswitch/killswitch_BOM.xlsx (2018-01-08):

Killswitch : Bill of Materials
Schematic Reference Number | Part Description | Manufacturer Part Number | Digikey Part Number | Datasheet | Digikey Link | Price (CAD) | Quantity | Total Cost | Total Cost
JP1 | Output Terminal 3-pin Male Surface Mount | 1241150-3 | A110955CT-ND | http://www.te.com/commerce/DocumentDelivery/DDEController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 | https://www.digikey.ca/product-detail/en/te-connectivity-amp-connectors/1241150-3/A110955CT-ND/4142339 | $3.80 | 1 | $3.80 | $18.11
N/A | Hall Effect Sensor (Testing 1) | DRV5033FAQDBZR | 296-44589-1-ND | http://www.ti.com/lit/ds/symlink/drv5033.pdf | https://www.digikey.ca/product-detail/en/texas-instruments/DRV5033FAQDBZR/296-44589-1-ND/6136273 | $1.59 | 4 | $6.36
N/A | Hall Effect Sensor (Testing 2) | DRV5033FAEDBZRQ1 | 296-44895-1-ND | http://www.ti.com/lit/ds/symlink/drv5033-q1.pdf | https://www.digikey.ca/product-detail/en/texas-instruments/DRV5033FAEDBZRQ1/296-44895-1-ND/6227343 | $1.73 | 4 | $6.92
C1, C4 | Capacitor (for price of 10) 2.2uF 0805 | CC0805ZRY5V6BB225 | 311-3446-1-ND | http://www.yageo.com/documents/recent/UPY-GPHC_Y5V_6.3V-to-50V_8.pdf | https://www.digikey.ca/product-detail/en/yageo/CC0805ZRY5V6BB225/311-3446-1-ND/7164467 | $0.10 | 2 | $0.19
~~C2, C3,C5,C6~~ | ~~Capacitor (for price of 10) 0.47uF 0603~~ | ~~CL10F474ZB8NNNC~~ | ~~1276-2377-1-ND~~ | ~~http://www.samsungsem.com/kr/support/product-search/mlcc/__icsFiles/afieldfile/2016/08/18/S_CL10F474ZB8NNNC.pdf~~ | ~~https://www.digikey.ca/product-detail/en/samsung-electro-mechanics/CL10F474ZB8NNNC/1276-2377-1-ND/3890463~~ | ~~$0.05~~ | ~~4~~
C2, C3,C5,C6 | Capacitor (for price of 10) 0.47uF 0603 | CGB3B3X5R1E474K055AB | 445-13240-1-ND | https://product.tdk.com/info/en/catalog/spec/mlccspec_commercial_lowprofile_en.pdf | https://www.digikey.ca/product-detail/en/tdk-corporation/CGB3B3X5R1E474K055AB/445-13240-1-ND/3954906 | $0.21 | 4 | $0.84
Notes: | We only actually need 1 of the Hall Effect Sensor types. We are testing two different types
 | Capacitor brand is non-issue, and they have flexibility in what values they are. These are just coupling capacitors
 | The output Terminal 3-pin is actually in the projects club and does not need to be purchased.

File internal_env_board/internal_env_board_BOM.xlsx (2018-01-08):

Internal Sensor Board Parts
Shematic Reference Number | Part Description | Manufacturer Part Number | Datasheet | Price | Quantity | Total Cost
JP2 | DIL VERTICAL PC TAIL PIN HEADER 2x3 | M20-9980345 | https://cdn.harwin.com/pdfs/M20-998.pdf | 0.348 | 1 | 0.348
JP3 | DIL VERTICAL PC TAIL PIN HEADER 2x4 | M20-9980445 | https://cdn.harwin.com/pdfs/M20-998.pdf | 0.48 | 1 | 0.48
R1,2 | RES SMD 10K OHM 1% 1/4W 1206 | RC1206FR-0710KL | http://www.yageo.com/documents/recent/PYu-RC_Group_51_RoHS_L_7.pdf | 0.047 | 2 | 0.094
R3,4 | RES SMD 220 OHM 1% 1/8W 0805 | RC0805FR-07220RL | http://www.yageo.com/documents/recent/PYu-RC_Group_51_RoHS_L_7.pdf | 0.031 | 2 | 0.062
R5 | RES SMD 1K OHM 1% 1/8W 0805 | RC0805FR-071KL | http://www.yageo.com/documents/recent/PYu-RC_Group_51_RoHS_L_7.pdf | 0.034 | 1 | 0.034
C4,5 | CAP CER 10UF 16V X7R 0805 | CL21B106KOQNNNG | http://www.samsungsem.com/kr/support/product-search/mlcc/CL21B106KOQNNNG.jsp | 0.39 | 2 | 0.78
CON2,3 | CONN HEADER GH SIDE 3POS 1.25MM | SM03B-GHS-TB(LF)(SN) | http://www.jst-mfg.com/product/pdf/eng/eGH.pdf | 0.68 | 2 | 1.36
U3 | IC TXRX CAN FAULT PROT 8SOIC | TCAN1042HVDRQ1 | http://www.ti.com/lit/ds/symlink/tcan1042hgv-q1.pdf | 2.05 | 1 | 2.05
CON1 | CONN HEADER 2POS 4.2MM VERT TIN | 39281023 | http://www.molex.com/pdm_docs/sd/039281023_sd.pdf | 0.83 | 1 | 0.83
JP1,4 | SIL VERTICAL PC TAIL PIN HEADER 1x2 | M20-9990245 | https://cdn.harwin.com/pdfs/M20-999.pdf | 0.2 | 2 | 0.4
Teensy | CONN HEADER FMALE 14POS .1" GOLD | PPPC141LFBN-RC | http://www.sullinscorp.com/drawings/78_P(N)PxCxxxLFBN-RC,_10492-H.pdf | 1.28 | 2 | 2.56
3V3, 5V | LED GREEN CLEAR 1206 SMD | LTST-C150GKT | http://optoelectronics.liteon.com/upload/download/DS-22-98-0004/LTST-C150GKT.pdf | 0.46 | 2 | 0.92
DANGER | LED RED CLEAR 1206 SMD | LTST-C150EKT | https://media.digikey.com/pdf/Data%20Sheets/Lite-On%20PDFs/LTST-C150EKT.pdf | 0.5 | 1 | 0.5
R6,8 | RES SMD 240 OHM 1% 1/4W 1206 | RC1206FR-07240RL | http://www.yageo.com/documents/recent/PYu-RC_Group_51_RoHS_L_7.pdf | 0.047 | 2 | 0.094
R9 | RES SMD 576 OHM 1% 1/4W 1206 | RC1206FR-07576RL | http://www.yageo.com/documents/recent/PYu-RC_Group_51_RoHS_L_7.pdf | 0.047 | 1 | 0.047
U2 | IC ALTIMETER I2C VERSION 8LGA | MPL3115A2R1 | https://media.digikey.com/pdf/Data%20Sheets/NXP%20PDFs/MPL3115A2.pdf | 6.96 | 1 | 6.96
HIH71201 | SENS HUMID/TEMP 3.3V I2C 3% 4SIP | HIH7120-021-001 | http://sensing.honeywell.com/index.php?ci_id=147071 | 14.73 | 1 | 14.73
HIH71201 | CONN RCPT 4POS T/H 1.27MM GOLD | M52-5000445 | https://cdn.harwin.com/pdfs/M52-500.pdf | 0.83 | 1 | 0.83
C1,3 | CAP CER 0.1UF 50V Y5V 1206 | CL31F104MBCNNNC | http://www.samsungsem.com/kr/support/product-search/mlcc/CL31F104MBCNNNC.jsp | 0.14 | 2 | 0.28
C2 | CAP CER 10UF 16V X7R 1206 | CL31B106MOHNNNE | http://www.samsungsem.com/kr/support/product-search/mlcc/CL31B106MOHNNNE.jsp | 0.21 | 1 | 0.21
R7 | RES SMD 82K OHM 5% 1/4W 1206 | RC1206JR-0782KL | http://www.yageo.com/documents/recent/PYu-RC_Group_51_RoHS_L_8.pdf | 0.15 | 1 | 0.15
CON4-7 | CONN HEADER GH SIDE 2POS 1.25MM | SM02B-GHS-TB(LF)(SN) | http://www.jst-mfg.com/product/pdf/eng/eGH.pdf | 0.46 | 4 | 1.84

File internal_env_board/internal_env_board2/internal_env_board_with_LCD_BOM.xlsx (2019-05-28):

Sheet: Board Components
Schematic Reference Number | Part Description | Manufacturer Part Number | Datasheet | Price | Quantity | Total Cost | Customer Reference
JP2 | DIL VERTICAL PC TAIL PIN HEADER 2x3 | M20-9980345 | https://cdn.harwin.com/pdfs/M20-998.pdf | $0.35 | 1 | $0.35 | INT_ENV
JP3 | DIL VERTICAL PC TAIL PIN HEADER 2x4 | M20-9980445 | https://cdn.harwin.com/pdfs/M20-998.pdf | $0.48 | 1 | $0.48 | INT_ENV
R1,2 | RES SMD 10K OHM 1% 1/4W 1206 | RC1206FR-0710KL | http://www.yageo.com/documents/recent/PYu-RC_Group_51_RoHS_L_7.pdf | $0.05 | 2 | $0.09 | INT_ENV
R3,4 | RES SMD 220 OHM 1% 1/8W 0805 | RC0805FR-07220RL | http://www.yageo.com/documents/recent/PYu-RC_Group_51_RoHS_L_7.pdf | $0.03 | 2 | $0.06 | INT_ENV
R5 | RES SMD 1K OHM 1% 1/8W 0805 | RC0805FR-071KL | http://www.yageo.com/documents/recent/PYu-RC_Group_51_RoHS_L_7.pdf | $0.03 | 1 | $0.03 | INT_ENV
C4,5 | CAP CER 10UF 16V X7R 0805 | CL21B106KOQNNNG | http://www.samsungsem.com/kr/support/product-search/mlcc/CL21B106KOQNNNG.jsp | $0.39 | 2 | $0.78 | INT_ENV
CON2,3 | CONN HEADER GH SIDE 3POS 1.25MM | SM03B-GHS-TB(LF)(SN) | http://www.jst-mfg.com/product/pdf/eng/eGH.pdf | $0.68 | 2 | $1.36 | INT_ENV
U3 | IC TXRX CAN FAULT PROT 8SOIC | TCAN1042HVDRQ1 | http://www.ti.com/lit/ds/symlink/tcan1042hgv-q1.pdf | $2.05 | 1 | $2.05 | INT_ENV
CON1 | CONN HEADER 2POS 4.2MM VERT TIN | 39281023 | http://www.molex.com/pdm_docs/sd/039281023_sd.pdf | $0.83 | 1 | $0.83 | INT_ENV
JP1,4 | SIL VERTICAL PC TAIL PIN HEADER 1x2 | M20-9990245 | https://cdn.harwin.com/pdfs/M20-999.pdf | $0.20 | 2 | $0.40 | INT_ENV
Teensy | CONN HEADER FMALE 14POS .1" GOLD | PPPC141LFBN-RC | http://www.sullinscorp.com/drawings/78_P(N)PxCxxxLFBN-RC,_10492-H.pdf | $1.28 | 2 | $2.56 | INT_ENV
3V3, 5V | LED GREEN CLEAR 1206 SMD | LTST-C150GKT | http://optoelectronics.liteon.com/upload/download/DS-22-98-0004/LTST-C150GKT.pdf | $0.46 | 2 | $0.92 | INT_ENV
DANGER | LED RED CLEAR 1206 SMD | LTST-C150EKT | https://media.digikey.com/pdf/Data%20Sheets/Lite-On%20PDFs/LTST-C150EKT.pdf | $0.50 | 1 | $0.50 | INT_ENV
R6,8 | RES SMD 240 OHM 1% 1/4W 1206 | RC1206FR-07240RL | http://www.yageo.com/documents/recent/PYu-RC_Group_51_RoHS_L_7.pdf | $0.05 | 2 | $0.09 | INT_ENV
R9 | RES SMD 576 OHM 1% 1/4W 1206 | RC1206FR-07576RL | http://www.yageo.com/documents/recent/PYu-RC_Group_51_RoHS_L_7.pdf | $0.05 | 1 | $0.05 | INT_ENV
U2 | IC ALTIMETER I2C VERSION 8LGA | MPL3115A2R1 | https://media.digikey.com/pdf/Data%20Sheets/NXP%20PDFs/MPL3115A2.pdf | $6.96 | 1 | $6.96 | INT_ENV
HIH71201 | SENS HUMID/TEMP 3.3V I2C 3% 4SIP | HIH7120-021-001 | http://sensing.honeywell.com/index.php?ci_id=147071 | $14.73 | 1 | $14.73 | INT_ENV
HIH71201 | CONN RCPT 4POS T/H 1.27MM GOLD | M52-5000445 | https://cdn.harwin.com/pdfs/M52-500.pdf | $0.83 | 1 | $0.83 | INT_ENV
C1,3 | CAP CER 0.1UF 50V Y5V 1206 | CL31F104MBCNNNC | http://www.samsungsem.com/kr/support/product-search/mlcc/CL31F104MBCNNNC.jsp | $0.14 | 2 | $0.28 | INT_ENV
C2 | CAP CER 10UF 16V X7R 1206 | CL31B106MOHNNNE | http://www.samsungsem.com/kr/support/product-search/mlcc/CL31B106MOHNNNE.jsp | $0.21 | 1 | $0.21 | INT_ENV
R7 | RES SMD 82K OHM 5% 1/4W 1206 | RC1206JR-0782KL | http://www.yageo.com/documents/recent/PYu-RC_Group_51_RoHS_L_8.pdf | $0.15 | 1 | $0.15 | INT_ENV
CON4-7 | CONN HEADER GH SIDE 2POS 1.25MM | SM02B-GHS-TB(LF)(SN) | http://www.jst-mfg.com/product/pdf/eng/eGH.pdf | $0.46 | 4 | $1.84 | INT_ENV
IC1 | IC SHIFT REGISTER 8BIT 16SOIC | 74HC595D,118 | https://assets.nexperia.com/documents/data-sheet/74HC_HCT595.pdf | $0.65 | 1 | $0.65 | INT_ENV
R11-R16 | RES SMD 560 OHM 5% 1/8W 0805 | RC0805JR-07560RL | RC Series, L Datasheet (http://www.yageo.com/documents/recent/PYu-RC_Group_51_RoHS_L_9.pdf) | $0.15 | 6 | $0.90 | INT_ENV
R22 | TRIMMER 20KOHM 0.25W J LEAD SIDE | SM-42TA203 | SM-42 & 43 Series Datasheet (https://www.nidec-copal-electronics.com/e/catalog/trimmer/sm-42&sm-43.pdf) | $5.20 | 1 | $5.20 | INT_ENV
JP5 | CONN HEADER 16 POS 2.54 | 61301611121 | 6130xx11121 Drawing (https://katalog.we-online.de/em/datasheet/6130xx11121.pdf) | $1.29 | 1 | $1.29 | INT_ENV
C6 | CAP CER 0.1UF 50V Y5V 0805 | CL21F104ZBCNNNC | http://www.samsungsem.com/kr/support/product-search/mlcc/__icsFiles/afieldfile/2018/07/03/CL21F104ZBCNNNC.pdf | $0.14 | 1 | $0.14 | INT_ENV
N/A (LCDs) | STANDARD LCD 16X2 + EXTRAS | 181 | TC1602A-09T (https://cdn-shop.adafruit.com/product-files/181/p181.pdf) | $14.28 | 1 | $14.28 | INT_ENV
R17 | RES 10 OHM 1% 1/4W 0805 | RNCP0805FTD10R0 | https://www.seielect.com/Catalog/SEI-rncp.pdf | $0.15 | 1 | $0.15 | INT_ENV
R10 | RES SMD 1M OHM 0.1% 1/8W 0805 | ERA-6AEB105V | https://industrial.panasonic.com/cdbs/www-data/pdf/RDM0000/AOA0000C307.pdf | $0.55 | 1 | $0.55 | INT_ENV
R18 | RES SMD 62 OHM 5% 1/2W 0805 | ERJ-P06J620V | https://industrial.panasonic.com/cdbs/www-data/pdf/RDO0000/AOA0000C331.pdf | $0.20 | 1 | $0.20 | INT_ENV
JP6 | 02+02 DIL VERT PIN HDR | M20-9760246 | M20-976yyyy Drawing (https://cdn.harwin.com/pdfs/M20-976.pdf) | $0.27 | 1 | $0.27 | INT_ENV
T1 | MOSFET N-CH 20V 2.3A SOT23 | BSS806NH6327XTSA1 | https://www.infineon.com/dgdl/BSS806N_Rev2.3_.pdf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 | $0.73 | 1 | $0.73 | INT_ENV
Total |  |  |  |  |  | $59.92

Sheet: Parts for Testing
Components for Testing | Part Description | Manufacturer Part Number | Datasheet | Price | Quantity | Total Cost | Customer Reference
IC1 | IC 8-BIT SHIFT REGISTER 16-DIP | SN74HC595N | SN54/SN74HC595 | $0.80 | 1 | $0.80 | INT_ENV
R11 - R16 | RES 560 OHM 1/4W 5% AXIAL | CF14JT560R | https://www.seielect.com/Catalog/SEI-CF_CFM.pdf | $0.15 | 6 | $0.90 | INT_ENV
C6 | CAP CER 0.1UF 50V X7R RADIAL | K104K10X7RF5UH5 | K Series Datasheet (http://www.vishay.com/docs/45171/kseries.pdf) | $0.33 | 1 | $0.33 | INT_ENV
N/A | CBL RIBN 20COND MULTICOLOR 5' | 111-2413-020 | N/A | $22.01 | 1 | $22.01 | INT_ENV
N/A | CONN RECEPT 16POS 24AWG MTA100 | 4-643814-6 | 643814 (https://www.te.com/commerce/DocumentDelivery/DDEController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) | $4.54 | 2 | $9.08 | INT_ENV
N/A | CONN COVER STRAIN RELIEF 16 POS | 1-643075-6 | 643075 (https://www.te.com/commerce/DocumentDelivery/DDEController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) | $1.31 | 2 | $2.62 | INT_ENV
R18 | RES 62 OHM 1/2W 5% AXIAL | CFR-50JB-52-62R | http://www.yageo.com/NewPortal/yageodocoutput?fileName=/pdf/throughhole/Yageo_LR_CFR_2013.pdf | $0.17 | 1 | $0.17 | INT_ENV
R17 | RES 10 OHM 2W 5% AXIAL | FW20A10R0JA | CF, CFM Series (https://www.seielect.com/Catalog/SEI-CF_CFM.pdf) | $0.83 | 1 | $0.83 | INT_ENV
R10 | RES 1M OHM 1W 5% AXIAL | VR68000001004JAC00 | http://www.vishay.com/docs/28907/vr25vr37vr68.pdf | $1.12 | 1 | $1.12 | INT_ENV
T1 | MOSFET N-CH 20V 530MA TO92-3 | TN0702N3-G | http://www.microchip.com/mymicrochip/filehandler.aspx?ddocname=en570658 | $1.56 | 1 | $1.56 | INT_ENV
R22 | TRIMMER 20K OHM 0.5W PC PIN TOP | 3362P-1-203LF | 3362 Series | $1.56 | 1 | $1.56 | INT_ENV
N/A | AMP SHUNT ASS'Y | 1-881545-1 | 881545 Drawing | $0.44 | 1 | $0.44 | INT_ENV
Total |  |  |  |  |  | $41.42

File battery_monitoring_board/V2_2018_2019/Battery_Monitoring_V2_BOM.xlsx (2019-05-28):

Teensy+i2c+CAN part list
Shematic Reference Number | Part Description | Manufacturer Part Number | Datasheet | Price | Quantity Required | On hand | Quantity To Buy | Total Cost | Customer Reference
JP5 | DIL VERTICAL PC TAIL PIN HEADER 2x3 | M20-9980345 | https://cdn.harwin.com/pdfs/M20-998.pdf | 0.348 | 1 |  | 1 | 0.348 | BATT_MON
JP6 | DIL VERTICAL PC TAIL PIN HEADER 2x4 | M20-9980445 | https://cdn.harwin.com/pdfs/M20-998.pdf | 0.48 | 1 |  | 1 | 0.48 | BATT_MON
R14, R15 | RES SMD 10K OHM 1% 1/4W 1206 | RC1206FR-0710KL | http://www.yageo.com/documents/recent/PYu-RC_Group_51_RoHS_L_7.pdf | 0.047 | 2 |  | 2 | 0.094 | BATT_MON
R16, R17 | RES SMD 220 OHM 1% 1/8W 0805 | RC0805FR-07220RL | http://www.yageo.com/documents/recent/PYu-RC_Group_51_RoHS_L_7.pdf | 0.031 | 2 |  | 2 | 0.062 | BATT_MON
R18 | RES SMD 1K OHM 1% 1/8W 0805 | RC0805FR-071KL | http://www.yageo.com/documents/recent/PYu-RC_Group_51_RoHS_L_7.pdf | 0.034 | 1 |  | 1 | 0.034 | BATT_MON
C3, C4 | CAP CER 10UF 16V X7R 0805 | CL21B106KOQNNNG | http://www.samsungsem.com/kr/support/product-search/mlcc/CL21B106KOQNNNG.jsp | 0.39 | 2 |  | 2 | 0.78 | BATT_MON
CON3 | CONN HEADER GH SIDE 3POS 1.25MM | SM03B-GHS-TB(LF)(SN) | http://www.jst-mfg.com/product/pdf/eng/eGH.pdf | 0.68 | 2 | 4 | 0 | 1.36 | BATT_MON
U4 | IC TXRX CAN FAULT PROT 8SOIC | TCAN1042HVDRQ1 | http://www.ti.com/lit/ds/symlink/tcan1042hgv-q1.pdf | 2.05 | 1 |  | 1 | 2.05 | BATT_MON | Part appears in multiple lists on this board
CON1 | CONN HEADER 2POS 4.2MM VERT TIN | 39281023 | http://www.molex.com/pdm_docs/sd/039281023_sd.pdf | 0.83 | 1 |  | 1 | 0.83 | BATT_MON
JP4 | SIL VERTICAL PC TAIL PIN HEADER 1x2 | M20-9990245 | https://cdn.harwin.com/pdfs/M20-999.pdf | 0.2 | 1 |  | 1 | 0.2 | BATT_MON | We have these parts on hand
Teensy | CONN HEADER FMALE 14POS .1" GOLD | PPPC141LFBN-RC | http://www.sullinscorp.com/drawings/78_P(N)PxCxxxLFBN-RC,_10492-H.pdf | 1.28 | 2 |  | 2 | 2.56 | BATT_MON
Battery Monitoring part List
Shematic Reference Number | Part Description | Manufacturer Part Number | Datasheet | Price | Quantity Required | On hand | Quantity To Buy | Total Cost | Customer Reference
U1, U2 | IC CURRENT SHUNT MONITOR 16VQFN | INA3221AIRGVR | http://www.ti.com/lit/ds/symlink/ina3221.pdf | 5.39 | 2 |  | 2 | 10.78 | BATT_MON
R4, R8, R12, R13 | RES 0.001 OHM 1% 5W 3920 | HCS3920FT1L00 | https://www.seielect.com/catalog/sei-hcs.pdf | 2.51 | 4 |  | 4 | 10.04 | BATT_MON
Q4, Q5, Q6 | MOSFET N-CH 30V 120A D2PAK | PSMN1R5-30BLEJ | https://assets.nexperia.com/documents/data-sheet/PSMN1R5-30BLE.pdf | 4.63 | 3 |  | 3 | 13.89 | BATT_MON
Q1, Q2, Q3 | OPTOISOLTR 5KV DARLINGTON 4-SOP | TCLD1000 | http://www.vishay.com/docs/83516/tcld1000.pdf | 1.09 | 3 |  | 3 | 3.27 | BATT_MON
D1, D2, D3 | DIODE ZENER 10V 500MW SOD123 | BZT52C10-7-F | https://www.diodes.com/assets/Datasheets/ds18004.pdf | 0.32 | 3 |  | 3 | 0.96 | BATT_MON
C1, C2 | CAP CER 0.1UF 50V Y5V 0805 | CL21F104ZBCNNNC | https://media.digikey.com/pdf/Data%20Sheets/Samsung%20PDFs/CL_Series_MLCC_ds.pdf | 0.14 | 2 | 7 | 0 | 0.28 | BATT_MON
R1, R2, R3 | RES SMD 1K OHM 5% 1/8W 0805 | RC2012J102CS | http://www.samsungsem.com/kr/support/product-search/chip-resistor/__icsFiles/afieldfile/2015/05/18/RC_DataSheet_(150330).pdf | 0.15 | 3 |  | 3 | 0.45 | BATT_MON
R5, R6, R7 | RES SMD 1K OHM 5% 1/4W 1206 | RC3216J102CS | http://www.samsungsem.com/kr/support/product-search/chip-resistor/__icsFiles/afieldfile/2015/05/18/RC_DataSheet_(150330).pdf | 0.15 | 3 | 16 | 0 | 0.45 | BATT_MON
R9, R10, R11 | RES SMD 10K OHM 5% 1/4W 1206 | RC3216J103CS | http://www.samsungsem.com/kr/support/product-search/chip-resistor/__icsFiles/afieldfile/2015/05/18/RC_DataSheet_(150330).pdf | 0.15 | 3 |  | 3 | 0.45 | BATT_MON
JP1, JP3 | CONN HEADER FEMALE 2POS .1" GOLD | PPPC021LFBN-RC | http://sullinscorp.com/catalogs/101_PAGE114-115_.100_FEMALE_HDR.pdf | 0.45 | 2 |  | 2 | 0.9 | BATT_MON
JP2 | CONN HEADER FEMALE 3POS .1" GOLD | PPPC031LFBN-RC | http://sullinscorp.com/catalogs/101_PAGE114-115_.100_FEMALE_HDR.pdf | 0.51 | 1 |  | 1 | 0.51 | BATT_MON
J1-J9 | CONN TERM BLOCK 2POS 6.35MM PCB | 1714955 | https://media.digikey.com/pdf/Data%20Sheets/Phoenix%20Contact%20PDFs/1714955.pdf | 2.11 | 9 |  | 9 | 18.99 | BATT_MON
Hotswap Circuit
Shematic Reference Number | Part Description | Manufacturer Part Number | Datasheet | Price | Quantity Required | On hand | Quantity To Buy | Total Cost | Customer Reference
U5 | IC CTRLR DUAL PWRPATH 20QFN | LTC4418IUF#PBF | LTC4418IUF#PBF | 9.23 | 1 |  | 1 | 9.23 | BATT_MON
Q10,Q11,Q12,Q13 | MOSFET P-CH 30V 60A PPAK SO-8 | SI7145DP-T1-GE3 | http://www.vishay.com/docs/64814/si7145dp.pdf | 3.68 | 4 | 3 | 1 | 14.72 | BATT_MON
LED1,LED2 | LED BLUE CLEAR 2012 SMD | APTD2012LQBC/D | http://www.kingbrightusa.com/images/catalog/SPEC/APTD2012LQBC-D.pdf | 0.93 | 2 |  | 2 | 1.86 | BATT_MON
R22,R25 | RES SMD 249K OHM 1% 1/4W 1206 | RC1206FR-07249KL | http://www.yageo.com/documents/recent/PYu-RC_Group_51_RoHS_L_9.pdf | 0.15 | 2 |  | 2 | 0.3 | BATT_MON
R23,R26 | RES 12.4K OHM 1% 1/4W 0805 | RNCP0805FTD12K4 | https://www.seielect.com/Catalog/SEI-rncp.pdf | 0.1 | 2 |  | 2 | 0.2 | BATT_MON
R24,R27 | RES 9.09K OHM 1% 1/4W 0805 | RNCP0805FTD9K09 | https://www.seielect.com/Catalog/SEI-rncp.pdf | 0.1 | 2 |  | 2 | 0.2 | BATT_MON
R28 | RES SMD 158K OHM 0.5% 1/4W 0805 | ERJ-PB6D1583V | https://industrial.panasonic.com/cdbs/www-data/pdf/RDM0000/AOA0000C328.pdf | 0.25 | 1 |  | 1 | 0.25 | BATT_MON
R29,R30 | RES 2.32K OHM 1% 1/4W 0805 | RNCP0805FTD2K32 | https://www.seielect.com/Catalog/SEI-rncp.pdf | 0.1 | 2 |  | 2 | 0.2 | BATT_MON
C6,C7,C8,C9,C10 | CAP CER 0.1UF 50V X7R 0805 | 08055C104J4T2A | http://datasheets.avx.com/AutoMLCC.pdf | 0.27 | 5 |  | 5 | 1.35 | BATT_MON
C5 | CAP CER 1000PF 25V X7R 0805 | VJ0805Y102JXXPW1BC | https://www.vishay.com/docs/28548/vjw1bcbascomseries.pdf | 0.34 | 1 |  | 1 | 0.34 | BATT_MON
C11 | CAP CER 33UF 25V X5R 1206 | C3216X5R1E336M160AC | https://product.tdk.com/info/en/catalog/datasheets/mlcc_commercial_general_en.pdf | 1.94 | 0 |  | 0 | 0 | BATT_MON
Reverse Polarity Protection Element Part List
Shematic Reference Number | Part Description | Manufacturer Part Number | Datasheet | Price | Quantity Required | On hand | Quantity To Buy | Total Cost | Customer Reference
R19, R20, R21 | RES SMD 10K OHM 5% 1/4W 1206 | RC3216J103CS | http://www.samsungsem.com/kr/support/product-search/chip-resistor/__icsFiles/afieldfile/2015/05/18/RC_DataSheet_(150330).pdf | 0.15 | 3 |  | 3 | 0.45 | BATT_MON
Q7, Q8, Q9 | MOSFET P-CH 30V 60A PPAK SO-8 | SI7145DP-T1-GE3 | http://www.vishay.com/docs/64814/si7145dp.pdf | 3.68 | 3 |  | 3 | 11.04 | BATT_MON
 |  |  |  |  | Total |  |  | 109.908

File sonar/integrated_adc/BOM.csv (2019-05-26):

Description | Manufacturer Partno. | DigiKey Partno. | Unit Cost | Quantity | Cost | Notes | Board
IC MCU 32BIT 512KB FLASH 100LQFP | STM32F303VET6 | 497-15164-ND | 12.69 | 1 |  |  | INT-ADC
CRYSTAL 12.0000MHZ 8PF SMD | NX5032GA-12.000000MHZ-LN-CD-1 | 644-1034-1-ND | 1.02 | 1 |  |  | INT-ADC
IC ADC 10BIT 2.7V 1CH SOT23-5 | MCP3021A5T-E/OT | MCP3021A5T-E/OTCT-ND | 1.7 | 1 |  |  | INT-ADC
IC TXRX CAN 8SOIC | MCP2562T-E/SN | MCP2562T-E/SNCT-ND | 1.44 | 1 |  |  | INT-ADC
IC REG LINEAR 3.3V 600MA SOT25 | AP2112K-3.3TRG1 | AP2112K-3.3TRG1DICT-ND | 0.74 | 1 |  |  | INT-ADC
CONN HEADER SMD 10POS 1.27MM | FTSH-105-01-F-DV-007 | SAM9433-ND | 2.61 | 1 |  | Debug Header | INT-ADC
CONN HEADER R/A 7POS 2.54MM | 68016-207HLF | 609-5524-ND | 0.74 | 1 |  | ADC Inputs | INT-ADC
CONN HEADER R/A 6POS 2.54MM | 68016-206HLF | 609-3320-ND | 0.64 | 1 |  | UART Connector | INT-ADC
TEENSY HEADER KIT | PRT-13925 | 1568-1422-ND | 2.18 | 1 |  | Teensy headers – Could have bought all the connectors but honestly this is probably cheaper. | INT-ADC
RES SMD 10K OHM 5% 1/8W 0805 | RC0805JR-0710KL | 311-10KARCT-ND | 0.15 | 3 |  | Generic Resistor for pulling up/etc. | INT-ADC
CAP CER 8PF 50V C0G/NPO 0805 | CC0805DRNPO9BN8R0 | 311-1097-1-ND | 0.2 | 2 |  | For XTAL | INT-ADC
CAP CER 0.1UF 25V X7R 0805 | CC0805KRX7R8BB104 | 311-1141-1-ND | 0.23 | 13 |  | Digital Decoupling + CAN TXRX Decoupling + ADC Decoupling | INT-ADC
CAP CER 4.7UF 10V X5R 0805 | CC0805KKX5R6BB475 | 311-1863-1-ND | 0.53 | 1 |  | Digital Decoupling | INT-ADC
CAP CER 10000PF 50V X7R 0805 | CC0805KRX7R9BB103 | 311-1136-1-ND | 0.16 | 2 |  | Analog Decoupling | INT-ADC
CAP CER 1UF 25V Y5V 0805 | CC0805ZRY5V8BB105 | 311-1358-1-ND | 0.28 | 4 |  | Analog Decoupling + Power Decoupling | INT-ADC
CAP CER 10UF 10V Y5V 0805 | CC0805ZKY5V6BB106 | 311-1355-1-ND | 0.41 | 1 |  | ADC Decoupling | INT-ADC
OPTIONAL
CONN RCPT USB2.0 MICRO B SMD R/A | 10118194-0001LF | 609-4618-1-ND | 0.61 | 1 |  |  | INT-ADC
RES SMD 15 OHM 5% 1/8W 0805 | RC0805JR-0715RL | 311-15ARCT-ND | 0.15 | 2 |  | USB Termination Resistors | INT-ADC
SWITCH TACTILE SPST-NO 0.05A 12V | RS-187R05A2-DS MT RT | CKN10361CT-ND | 0.82 | 1 |  | Reset Button | INT-ADC
CONN HEADER VERT 3POS 2.54MM | 68000-103HLF | 609-3461-ND | 0.42 | 1 |  |  | INT-ADC
CONN JUMPER SHORTING .100" GOLD | QPC02SXGN-RC | S9337-ND | 0.15 | 1 |  | Boot selection stuff | INT-ADC
RES SMD 1.5K OHM 5% 1/8W 0805 | RC0805JR-071K5L | 311-1.5KARCT-ND | 0.15 | 1 |  | USB D+ Pullup | INT-ADC

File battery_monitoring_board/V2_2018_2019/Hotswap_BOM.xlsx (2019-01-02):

Hotswap Circuit
Shematic Reference Number | Part Description | Manufacturer Part Number | Datasheet | Price | Quantity | Total Cost
U1 | IC CTRLR DUAL PWRPATH 20QFN | LTC4418IUF#PBF | LTC4418IUF#PBF | 9.23 | 1 | 9.23
Q1,Q2.Q3,Q4 | MOSFET P-CH 30V 60A PPAK SO-8 | SI7145DP-T1-GE3 | http://www.vishay.com/docs/64814/si7145dp.pdf | 3.68 | 4 | 14.72
LED1,LED2 | LED BLUE CLEAR 2012 SMD | APTD2012LQBC/D | http://www.kingbrightusa.com/images/catalog/SPEC/APTD2012LQBC-D.pdf | 0.93 | 2 | 1.86
R1,R4 | RES SMD 249K OHM 1% 1/4W 1206 | RC1206FR-07249KL | http://www.yageo.com/documents/recent/PYu-RC_Group_51_RoHS_L_9.pdf | 0.15 | 2 | 0.3
R2,R5 | RES 12.4K OHM 1% 1/4W 0805 | RNCP0805FTD12K4 | https://www.seielect.com/Catalog/SEI-rncp.pdf | 0.1 | 2 | 0.2
R3,R6 | RES 9.09K OHM 1% 1/4W 0805 | RNCP0805FTD9K09 | https://www.seielect.com/Catalog/SEI-rncp.pdf | 0.1 | 2 | 0.2
R7 | RES SMD 158K OHM 0.5% 1/4W 0805 | ERJ-PB6D1583V | https://industrial.panasonic.com/cdbs/www-data/pdf/RDM0000/AOA0000C328.pdf | 0.25 | 1 | 0.25
R8,R9 | RES 2.32K OHM 1% 1/4W 0805 | RNCP0805FTD2K32 | https://www.seielect.com/Catalog/SEI-rncp.pdf | 0.1 | 2 | 0.2
C1,C2,C4,C5,C6 | CAP CER 0.1UF 50V X7R 0805 | 08055C104J4T2A | http://datasheets.avx.com/AutoMLCC.pdf | 0.27 | 5 | 1.35
C3 | CAP CER 1000PF 25V X7R 0805 | VJ0805Y102JXXPW1BC | https://www.vishay.com/docs/28548/vjw1bcbascomseries.pdf | 0.34 | 1 | 0.34
C7 | CAP CER 33UF 25V X5R 1206 | C3216X5R1E336M160AC | https://product.tdk.com/info/en/catalog/datasheets/mlcc_commercial_general_en.pdf | 1.94 | 1 | 1.94
 |  |  |  |  | Total | 28.65

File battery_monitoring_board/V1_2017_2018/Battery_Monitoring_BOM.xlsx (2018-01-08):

Teensy+i2c+CAN part list
Shematic Reference Number | Part Description | Manufacturer Part Number | Datasheet | Price | Quantity | Total Cost
JP5 | DIL VERTICAL PC TAIL PIN HEADER 2x3 | M20-9980345 | https://cdn.harwin.com/pdfs/M20-998.pdf | 0.348 | 1 | 0.348
JP6 | DIL VERTICAL PC TAIL PIN HEADER 2x4 | M20-9980445 | https://cdn.harwin.com/pdfs/M20-998.pdf | 0.48 | 1 | 0.48
R14, R15 | RES SMD 10K OHM 1% 1/4W 1206 | RC1206FR-0710KL | http://www.yageo.com/documents/recent/PYu-RC_Group_51_RoHS_L_7.pdf | 0.047 | 2 | 0.094
R16, R17 | RES SMD 220 OHM 1% 1/8W 0805 | RC0805FR-07220RL | http://www.yageo.com/documents/recent/PYu-RC_Group_51_RoHS_L_7.pdf | 0.031 | 2 | 0.062
R18 | RES SMD 1K OHM 1% 1/8W 0805 | RC0805FR-071KL | http://www.yageo.com/documents/recent/PYu-RC_Group_51_RoHS_L_7.pdf | 0.034 | 1 | 0.034
C3, C4 | CAP CER 10UF 16V X7R 0805 | CL21B106KOQNNNG | http://www.samsungsem.com/kr/support/product-search/mlcc/CL21B106KOQNNNG.jsp | 0.39 | 2 | 0.78
CON3 | CONN HEADER GH SIDE 3POS 1.25MM | SM03B-GHS-TB(LF)(SN) | http://www.jst-mfg.com/product/pdf/eng/eGH.pdf | 0.68 | 2 | 1.36
U4 | IC TXRX CAN FAULT PROT 8SOIC | TCAN1042HVDRQ1 | http://www.ti.com/lit/ds/symlink/tcan1042hgv-q1.pdf | 2.05 | 1 | 2.05
CON1 | CONN HEADER 2POS 4.2MM VERT TIN | 39281023 | http://www.molex.com/pdm_docs/sd/039281023_sd.pdf | 0.83 | 1 | 0.83
JP4 | SIL VERTICAL PC TAIL PIN HEADER 1x2 | M20-9990245 | https://cdn.harwin.com/pdfs/M20-999.pdf | 0.2 | 1 | 0.2
Teensy | CONN HEADER FMALE 14POS .1" GOLD | PPPC141LFBN-RC | http://www.sullinscorp.com/drawings/78_P(N)PxCxxxLFBN-RC,_10492-H.pdf | 1.28 | 2 | 2.56
Battery Monitoring part List
Shematic Reference Number | Part Description | Manufacturer Part Number | Datasheet | Price | Quantity | Total Cost
U1, U2 | IC CURRENT SHUNT MONITOR 16VQFN | INA3221AIRGVR | http://www.ti.com/lit/ds/symlink/ina3221.pdf | 5.39 | 2 | 10.78
R4, R8, R12, R13 | RES 0.001 OHM 1% 5W 3920 | HCS3920FT1L00 | https://www.seielect.com/catalog/sei-hcs.pdf | 2.51 | 4 | 10.04
Q4, Q5, Q6 | MOSFET N-CH 30V 120A D2PAK | PSMN1R5-30BLEJ | https://assets.nexperia.com/documents/data-sheet/PSMN1R5-30BLE.pdf | 4.63 | 3 | 13.89
Q1, Q2, Q3 | OPTOISOLTR 5KV DARLINGTON 4-SOP | TCLD1000 | http://www.vishay.com/docs/83516/tcld1000.pdf | 1.09 | 3 | 3.27
D1, D2, D3 | DIODE ZENER 10V 500MW SOD123 | BZT52C10-7-F | https://www.diodes.com/assets/Datasheets/ds18004.pdf | 0.32 | 3 | 0.96
C1, C2 | CAP CER 0.1UF 50V Y5V 0805 | CL21F104ZBCNNNC | https://media.digikey.com/pdf/Data%20Sheets/Samsung%20PDFs/CL_Series_MLCC_ds.pdf | 0.14 | 2 | 0.28
R1, R2, R3 | RES SMD 1K OHM 5% 1/8W 0805 | RC2012J102CS | http://www.samsungsem.com/kr/support/product-search/chip-resistor/__icsFiles/afieldfile/2015/05/18/RC_DataSheet_(150330).pdf | 0.15 | 3 | 0.45
R5, R6, R7 | RES SMD 1K OHM 5% 1/4W 1206 | RC3216J102CS | http://www.samsungsem.com/kr/support/product-search/chip-resistor/__icsFiles/afieldfile/2015/05/18/RC_DataSheet_(150330).pdf | 0.15 | 3 | 0.45
R9, R10, R11 | RES SMD 10K OHM 5% 1/4W 1206 | RC3216J103CS | http://www.samsungsem.com/kr/support/product-search/chip-resistor/__icsFiles/afieldfile/2015/05/18/RC_DataSheet_(150330).pdf | 0.15 | 3 | 0.45
JP1, JP3 | CONN HEADER FEMALE 2POS .1" GOLD | PPPC021LFBN-RC | http://sullinscorp.com/catalogs/101_PAGE114-115_.100_FEMALE_HDR.pdf | 0.45 | 2 | 0.9
JP2 | CONN HEADER FEMALE 3POS .1" GOLD | PPPC031LFBN-RC | http://sullinscorp.com/catalogs/101_PAGE114-115_.100_FEMALE_HDR.pdf | 0.51 | 1 | 0.51
J1-J8 | CONN TERM BLOCK 2POS 6.35MM PCB | 1714955 | https://media.digikey.com/pdf/Data%20Sheets/Phoenix%20Contact%20PDFs/1714955.pdf | 2.11 | 6 | 12.66
 |  |  |  |  | Total | 63.438

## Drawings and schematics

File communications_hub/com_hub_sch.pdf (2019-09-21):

# 10u GNDGND

# TCAN1042 U1 TCAN1042 U2

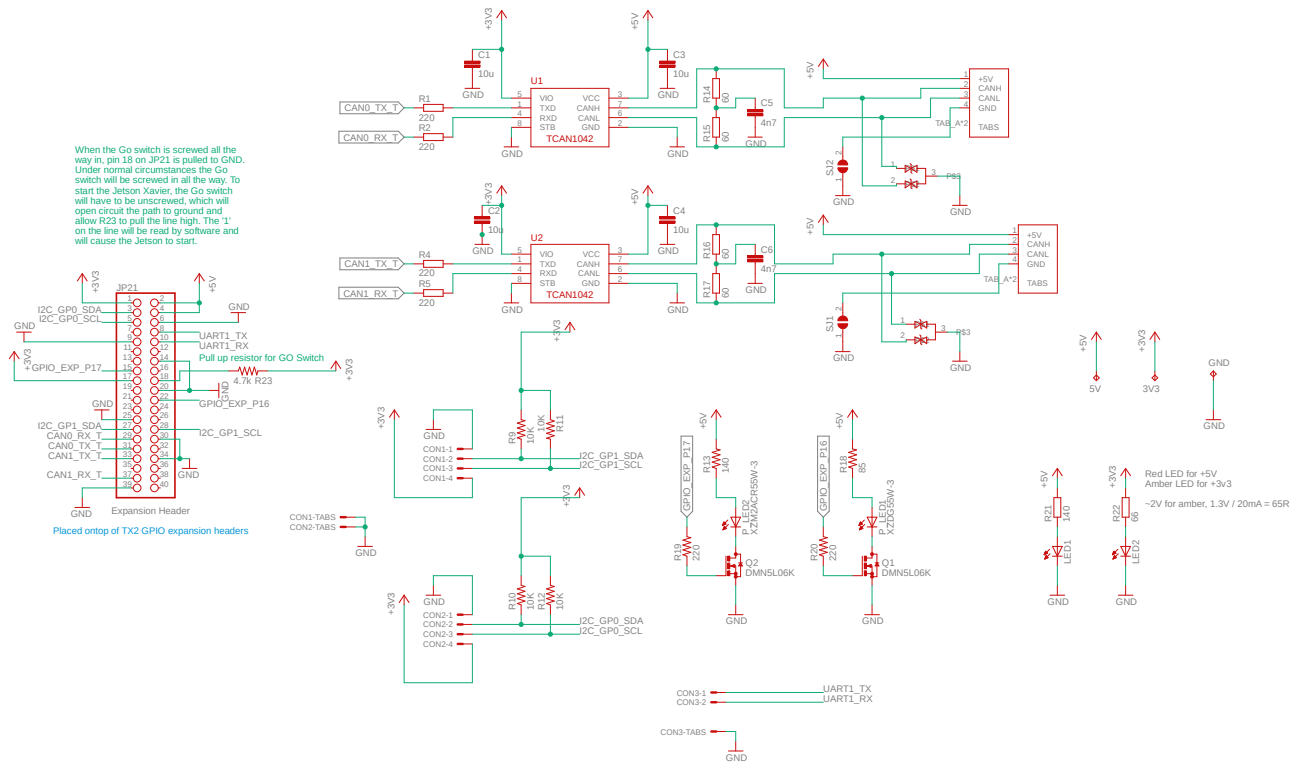
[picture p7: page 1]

When the Go switch is screwed all the
way in, pin 18 on JP21 is pulled to GND.
Under normal circumstances the Go
switch will be screwed in all the way. To
start the Jetson Xavier, the Go switch
will have to be unscrewed, which will
open circuit the path to ground and
allow R23 to pull the line high. The '1'
on the line will be read by software and
will cause the Jetson to start.

UART1_TX
UART1_RX
Pull up resistor for GO Switch

Placed ontop of TX2 GPIO expansion headers

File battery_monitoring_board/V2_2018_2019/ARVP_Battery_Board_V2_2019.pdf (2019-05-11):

2019-05-07 7:48 PM f=0.45 C:\Users\moira\Desktop\Repo\au_hardware\battery_monitoring_board\V2_2018_2019\Battery_Monitoring_V2.sch (Sheet: 1/2) GND | 0.001Ohm
0.001Ohm | 0.001Ohm
0.001Ohm GND 0.1microF | 0.1microF

# MKDS_5/2-6,352 MKDS_5/2-6,352 MKDS_5/2-6,352

MKDS_5/2-6,352 | MKDS_5/2-6,352 MKDS_5/2-6,352 MKDS_5/2-6,352

MKDS_5/2-6,352 GND

PSMN1R5-30BLE

PSMN1R5-30BLE

PSMN1R5-30BLE

1k1k1k ¹⁰k 10k 10k | 1k1k1k | GND | +5V GND

GND +3V³

220

220

10k 10k +3V³ | GND +5V | +3V³ | GND

10u GND

10u GND 1k GND | GND GND
GND GND GND ¹⁰k 10k 10k MKDS_5/2-6,352 | GND | SI7145DP SI7145DP SI7145DP

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
8 16151413

INA3221 | R⁸ R4

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
8 16151413

INA3221 | R¹³ R12 C¹ | C²

J4

J3

J2

J1

J5

J6

J7

J8 A

P$1 C1 | P$2 E
P$3 | C2 P$4 | A
P$1 C1 | P$2 E
P$3 | C2 P$4 | A
P$1 C1 | P$2 E
P$3 | C2 P$4 Q4 Q5 Q6
R1 R2 R3 R⁹ R¹⁰ R¹¹ | R5 R6 R7
CON1G$1 CON1G$2

1 2
3 4
5 6

JP5

2

1JP4 R16 R17 R15 R14

0/RX1/T

1/TX1/T

2
3.3V

3/CAN-TX/PWM

4/CAN-RX-PWM

5/PWM

6/PWM

7/RX3

8/TX3

9/RX2/PWM

10/TX2/PWM

11/MOSI 12/MISO

13/SCK/LED

14/A0

15/A1/T

16/A2/T

17/A3/T

18/A4/T/SDA0

19/A5/T/SCL0

20/A6/PWM

21/A7/PWM

22/A8/T/PWM

23/A9/T/PWM

# AGND GND

VIN | 1 2 3 4 5 6 7 8 JP⁶ | TXD 1 | GND | 2 VCC | 3 RXD 4 | VIO 5 | CANL | 6 CANH | 7 STB 8 C3 | C4 R¹⁸ | CON2-1 CON2-2 CON2-3 CON2-TABS CON3-1 CON3-2 CON3-3 CON3-TABS

1
2

JP1
1
2

# JP3 JP² 1

2

### 3 R21 R19 R20

J9 | Q⁹ Q⁷ Q¹⁴ BATTERY4_IN | WARNING_OUT | WARNING_OUT WARNING_OUT
CRITICAL_OUT | CRITICAL_OUT CRITICAL_OUT
PV_OUT | PV_OUT PV_OUT

TC_OUT
TC_OUT

TC_OUT

BATTERY1/2.2C

+5V/2.6D

+5V/2.6D

+5V/2.6D

+5V/2.6D

MOTOR1 MOTOR1 | MOTOR3 MOTOR3 | MOTOR2 MOTOR2 | POWER_BOARD

POWER_BOARD

+3V3 | +3V3 ⁺³V³ | +3V³ SDA

SDA

SDA

SCL SCL | SCL | VIN
CAN_RX_T CAN_TX_T | CAN_RX_T CAN_TX_T

WALL/2.3C

ELECTRONICS_BATTERY/2.6B

BATTERY_4 | BATTERY_4 | BATTERY_4 BATTERY_3 | BATTERY_3 | BATTERY_3 BATTERY3_IN
BATTERY_2 | BATTERY_2 BATTERY_2 BATTERY2_IN

## ARVP

TCAN1042 U4

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
1 | 2 | 3 | 4 | 5 | 6 | 7 | 8 | 9 | 10 | 11
Date: | Sheet: | REV: TITLE: Document Number: 2019-05-07 7:44 PM | 1/2 Battery_Monitoring_V2

3.3V

3.3V

Kill switch motor GND

INA3221 MONITORING

Otoisolators | OUTPUTS
MOSFET Kill | to SDA PIN

to SCL PIN

A jumper must be used on JP3 to use the the kill switch | Kill Switch Bypass

PMOS

The wall power terminal & the electronics battery pass through the hotswap IC(sheet 2) before going

to the INA then out the terminal to the power boar. This rail does not need to turn off with the kill switch and receives reverse voltage protection from the hotswap IC. | The INA3221s measure the voltage and current coming from the batteries an flowing through the sensing resistors (0.001Ohm)
| before leaving through the motor terminals. The sensing resistors must be connected using a Kelvin connection for the best results.

Jumpers must be used on JP4/JP5 to use the teensy & INAs

Jumpers must be used on JP4/JP5 to use the teensy & INAs Reverse polarity protection: The source of a PMOS is connected to the battery terminal (18V); since the gate (0V) must be less than the source by at least the

threshold voltage to conduct, the PMOS is always on until a negative voltage is applied. | Kill Switch: The kill switch uses darlington optioisolators and an NMOS to control
| the connection between the battery monitoring board GND and the motor
| terminal GNDs. When the magnet is in place, current is allowed to flow through the internal diode which turns on the internal BJTs of the optioisolator. This sets the gate
| of the NMOS to 10V and turns it on, connecting the GNDs. When the magnet is removed, no current flows
| through the diode side and there is therefore no conduction on the BJT side. The gate of the NMOS sits at zero and
| it remains off, preventing the GND connection and therefore any current
| flow to the motors.
UAVCAN Design Block Motor Battery Terminals | Motor Terminals | These INAs use addresses 1&2 in the ina code, check if any other
ina models are using the same addresses before connecting them to this teensy. The power monitoring board uses address 4

-> INA3221

A

A

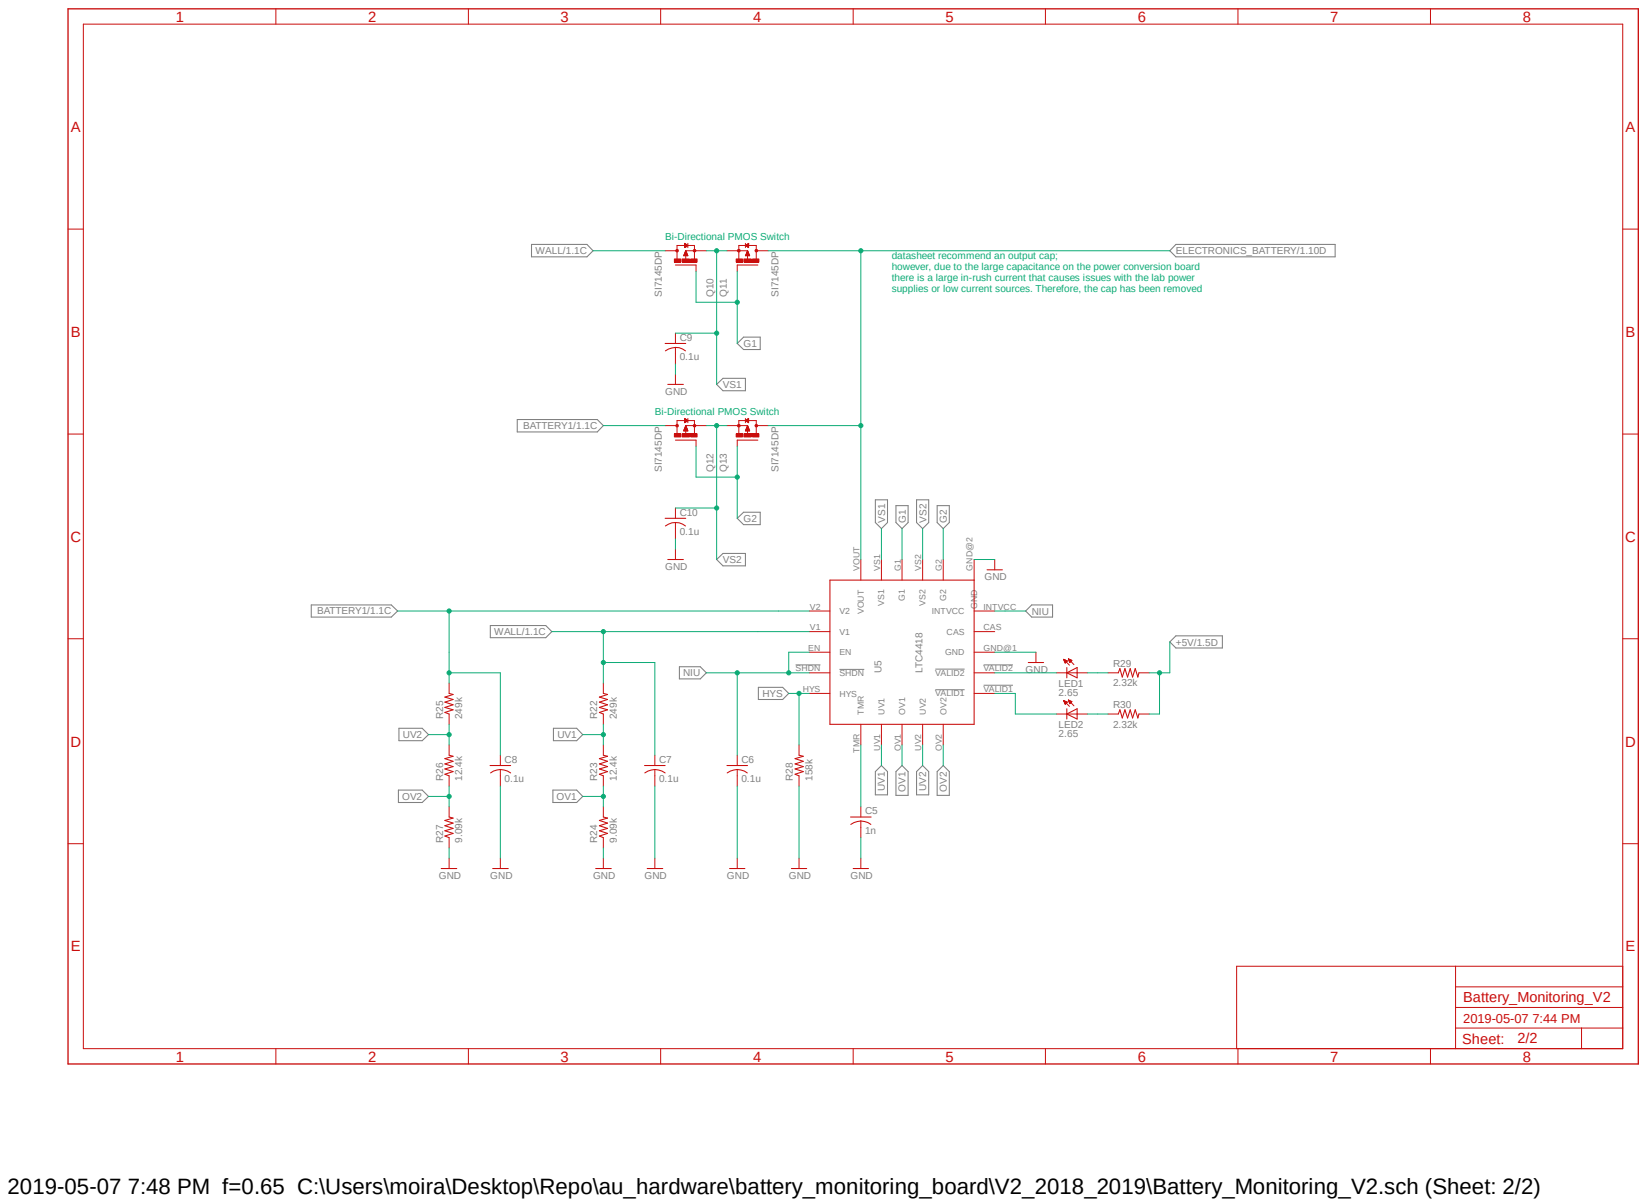
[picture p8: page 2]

Bi-Directional PMOS Switch

datasheet recommend an output cap; however, due to the large capacitance on the power conversion board

2019-05-07 7:48 PM f=0.65 C:\Users\moira\Desktop\Repo\au_hardware\battery_monitoring_board\V2_2018_2019\Battery_Monitoring_V2.sch (Sheet: 2/2)
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

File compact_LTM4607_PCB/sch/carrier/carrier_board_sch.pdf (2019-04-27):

A

A

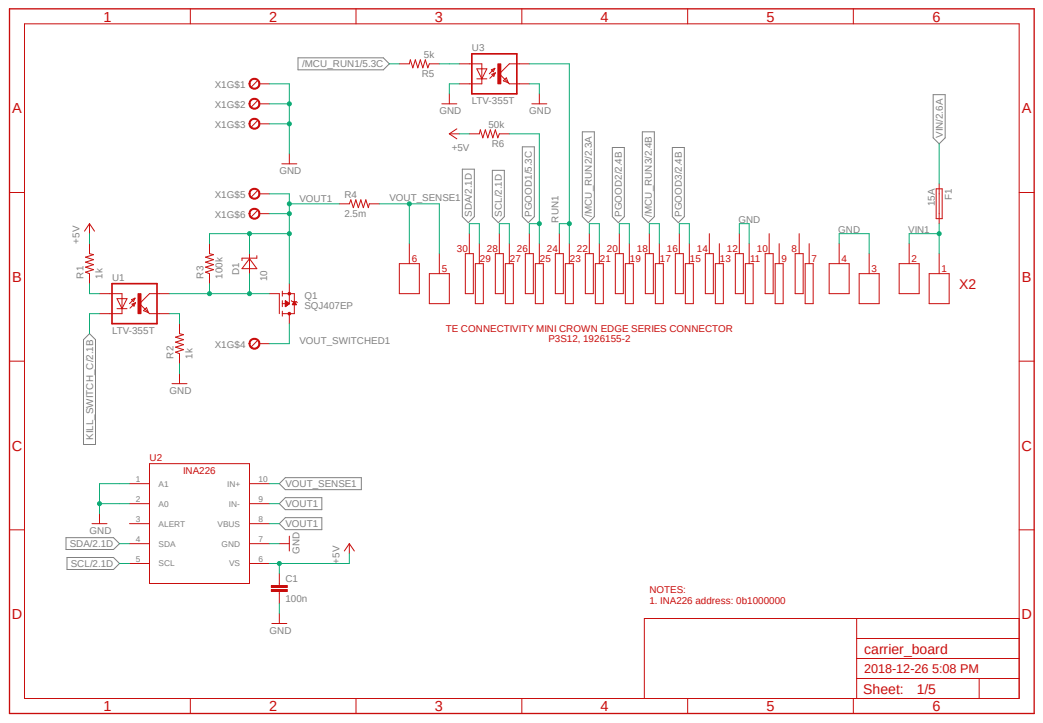
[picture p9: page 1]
GND GNDGND; GND; SQJ407EP; LTV-355T; ALERT 3; SDA 4; SCL 5; 6 GND; 7 VBUS; VOUT_SENSE1; PGOOD¹/5.3C; RUN¹; VOUT1; SDA/2.1D; SCL/2.1D; VOUT_SWITCHED1 KILL_SWITCH_C/2.1B; /MCU_RUN1/5.3C; VIN1; VIN/2.6A /MCU_RUN²/2.3A; PGOOD²/2.4B; /MCU_RUN³/2.4B; PGOOD³/2.4B; NOTES: 1. INA226 address: 0b1000000; Sheet:; carrier_board; INA226

TE CONNECTIVITY MINI CROWN EDGE SERIES CONNECTOR

# GND GND +5V

A

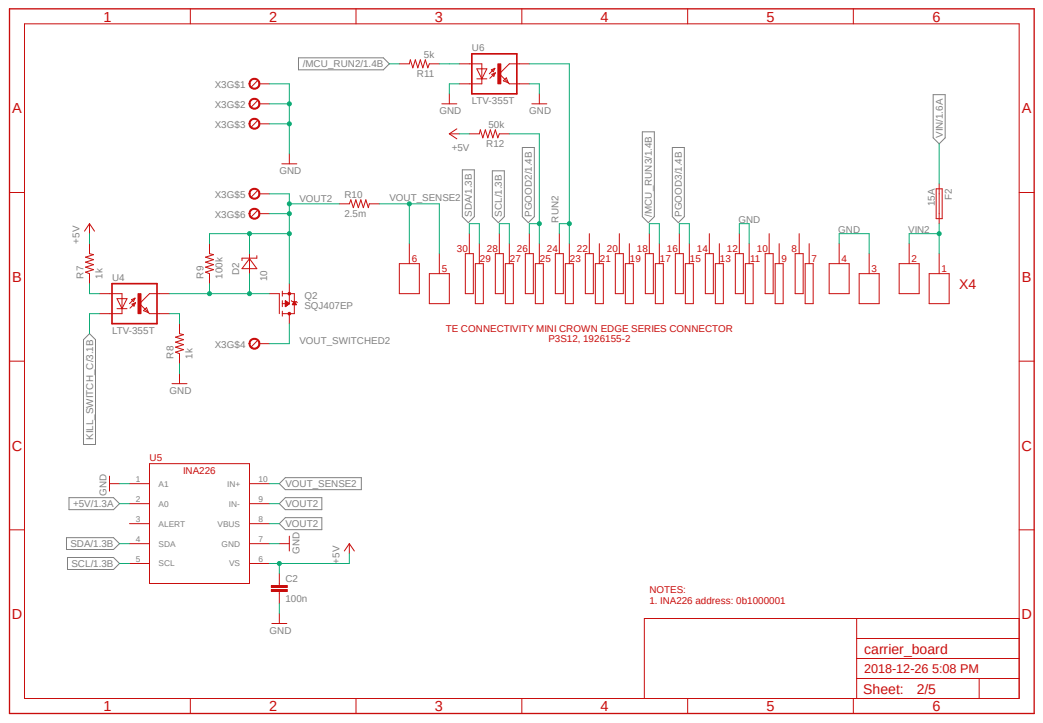
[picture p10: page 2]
GND; SQJ407EP; LTV-355T; ALERT 3; SDA 4; SCL 5; 6 GND; 7 VBUS; VOUT_SENSE2; PGOOD²/1.4B; RUN²; VOUT2; SDA/1.3B; SCL/1.3B; VOUT_SWITCHED2 KILL_SWITCH_C/3.1B; /MCU_RUN2/1.4B; VIN2; VIN/1.6A /MCU_RUN³/1.4B; PGOOD³/1.4B; NOTES: 1. INA226 address: 0b1000001; Sheet:; carrier_board; INA226

TE CONNECTIVITY MINI CROWN EDGE SERIES CONNECTOR

GND GND GND

# VIN3 VIN/2.6A

A

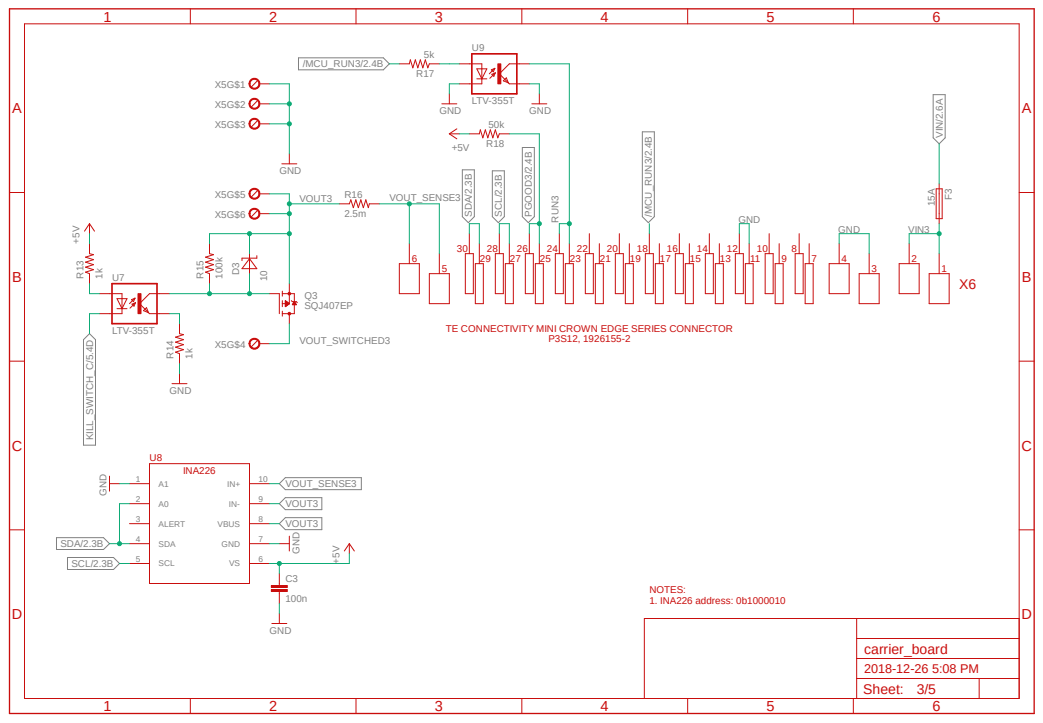
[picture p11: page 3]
GND; SQJ407EP; LTV-355T; ALERT 3; SDA 4; SCL 5; 6 GND; 7 VBUS; R¹⁵; D³ R¹⁴ R¹³; VOUT_SENSE3; PGOOD³/2.4B; RUN³; VOUT3; SDA/2.3B; SCL/2.3B; VOUT_SWITCHED3 KILL_SWITCH_C/5.4D; /MCU_RUN3/2.4B; /MCU_RUN³/2.4B; NOTES: 1. INA226 address: 0b1000010; Sheet:; carrier_board; INA226

TE CONNECTIVITY MINI CROWN EDGE SERIES CONNECTOR

GND GND GND

# C4 R²⁶

A

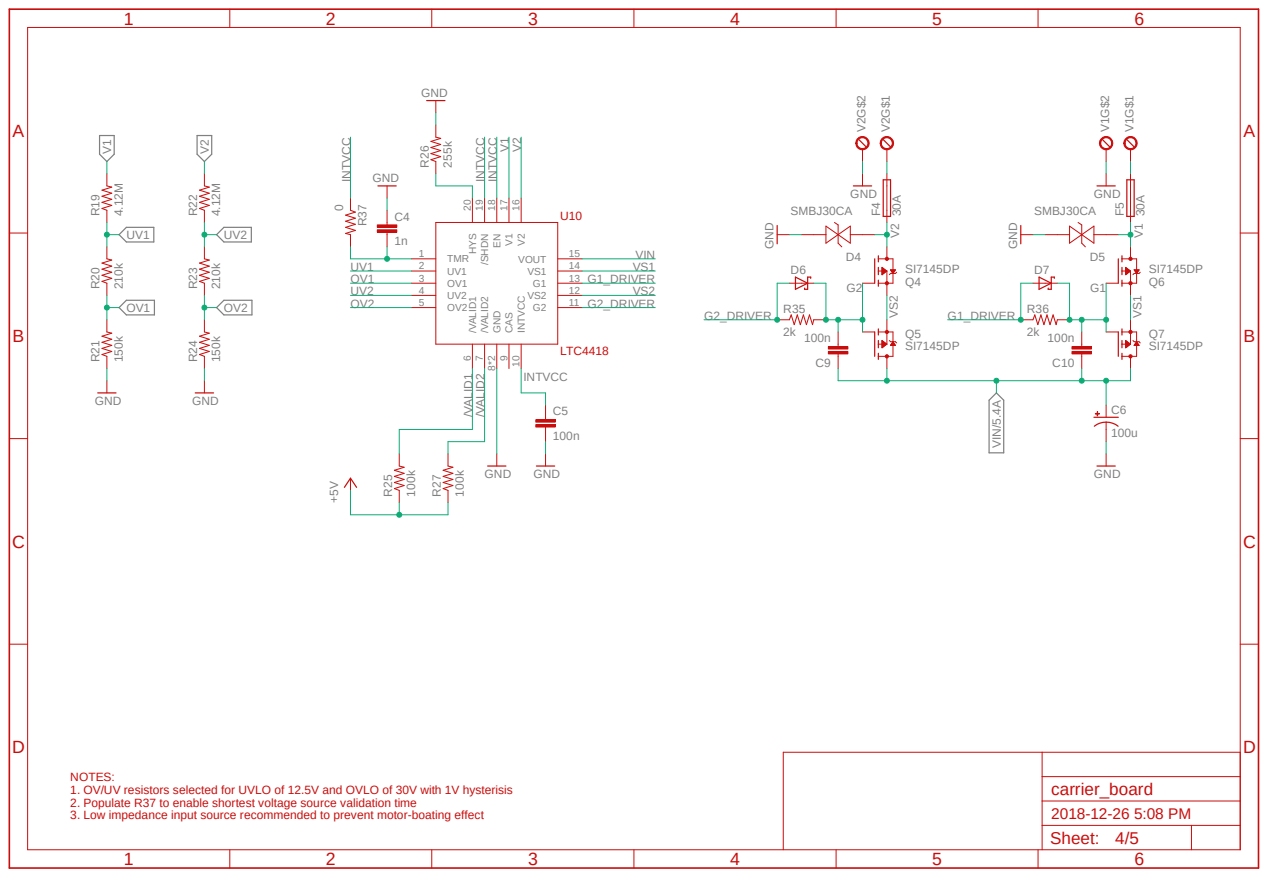
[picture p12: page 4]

9 INTVCC 10 G2 11 VS2 12 G1 13 VS1 14 VOUT 15 V2 16 V1 17 EN 18 /SHDN 19 HYS 20

NOTES:
1. OV/UV resistors selected for UVLO of 12.5V and OVLO of 30V with 1V hysterisis
2. Populate R37 to enable shortest voltage source validation time
3. Low impedance input source recommended to prevent motor-boating effect

A

A

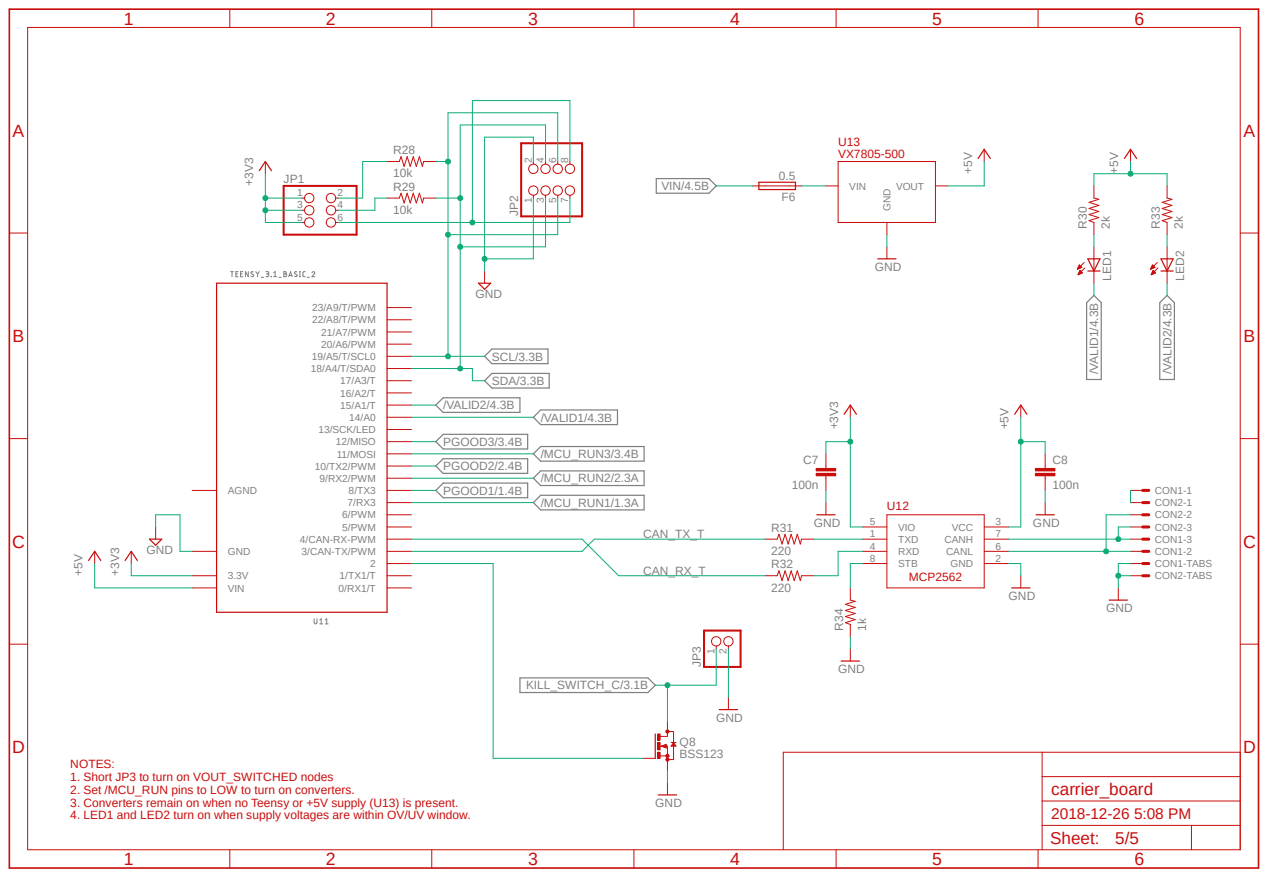
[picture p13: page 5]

NOTES:
1. Short JP3 to turn on VOUT_SWITCHED nodes
2. Set /MCU_RUN pins to LOW to turn on converters.
3. Converters remain on when no Teensy or +5V supply (U13) is present.
4. LED1 and LED2 turn on when supply voltages are within OV/UV window.

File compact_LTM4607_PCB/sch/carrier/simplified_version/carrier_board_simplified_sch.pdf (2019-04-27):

A

A

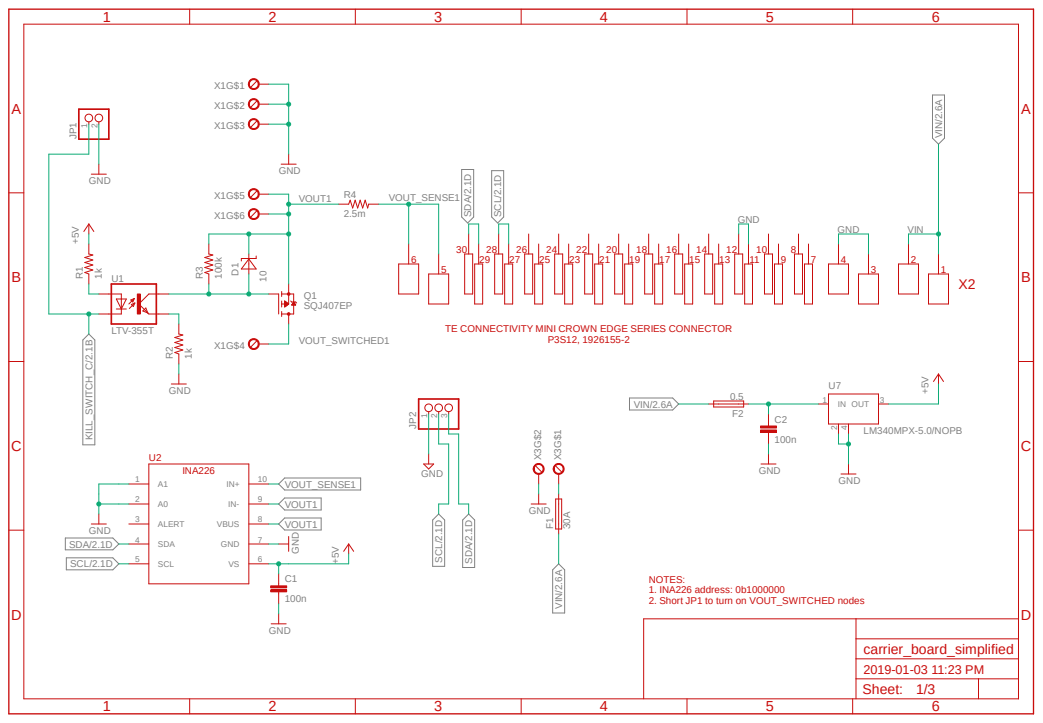
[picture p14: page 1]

TE CONNECTIVITY MINI CROWN EDGE SERIES CONNECTOR

1. INA226 address: 0b1000000
2. Short JP1 to turn on VOUT_SWITCHED nodes

A

A

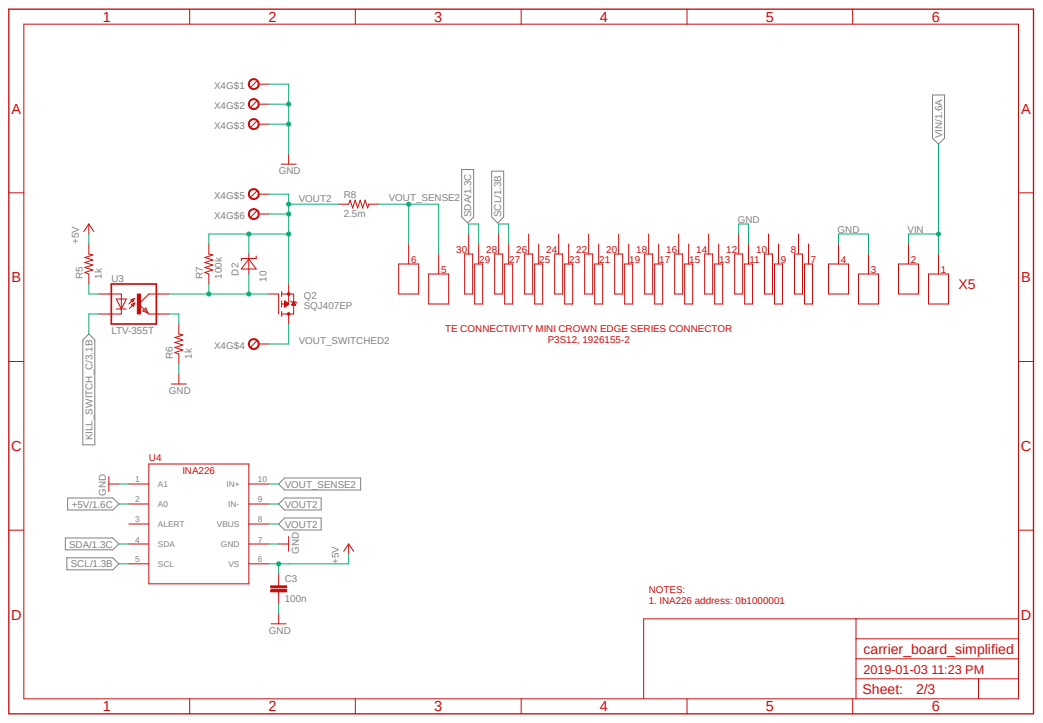
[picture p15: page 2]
GND; SQJ407EP; LTV-355T; ALERT 3; SDA 4; SCL 5; 6 GND; 7 VBUS; VOUT_SENSE2; VOUT2; SDA/1.3C; SCL/1.3B; VOUT_SWITCHED2 KILL_SWITCH_C/3.1B; VIN/1.6A; VIN; NOTES: 1. INA226 address: 0b1000001; Sheet:; carrier_board_simplified; INA226

TE CONNECTIVITY MINI CROWN EDGE SERIES CONNECTOR

GND GND GND

A

A

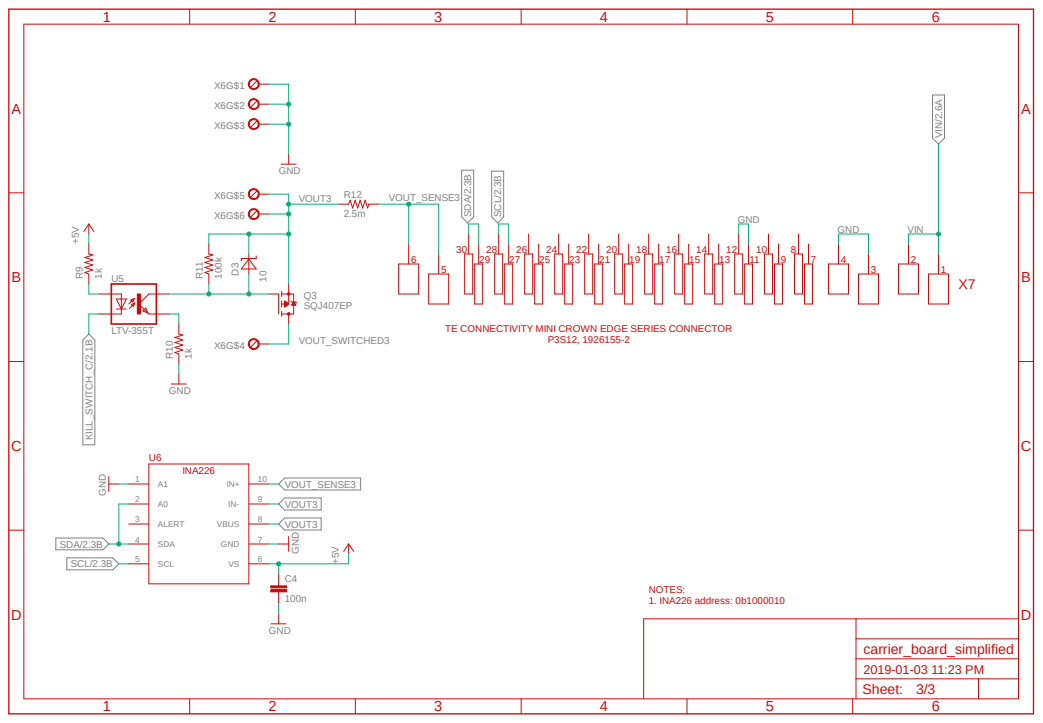
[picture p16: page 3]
GND; SQJ407EP; LTV-355T; ALERT 3; SDA 4; SCL 5; 6 GND; 7 VBUS; R¹¹; D³ R¹⁰ R⁹; VOUT_SENSE3; VOUT3; SDA/2.3B; SCL/2.3B; VOUT_SWITCHED3 KILL_SWITCH_C/2.1B; VIN/2.6A; VIN; NOTES: 1. INA226 address: 0b1000010; Sheet:; carrier_board_simplified; INA226

TE CONNECTIVITY MINI CROWN EDGE SERIES CONNECTOR

GND GND GND

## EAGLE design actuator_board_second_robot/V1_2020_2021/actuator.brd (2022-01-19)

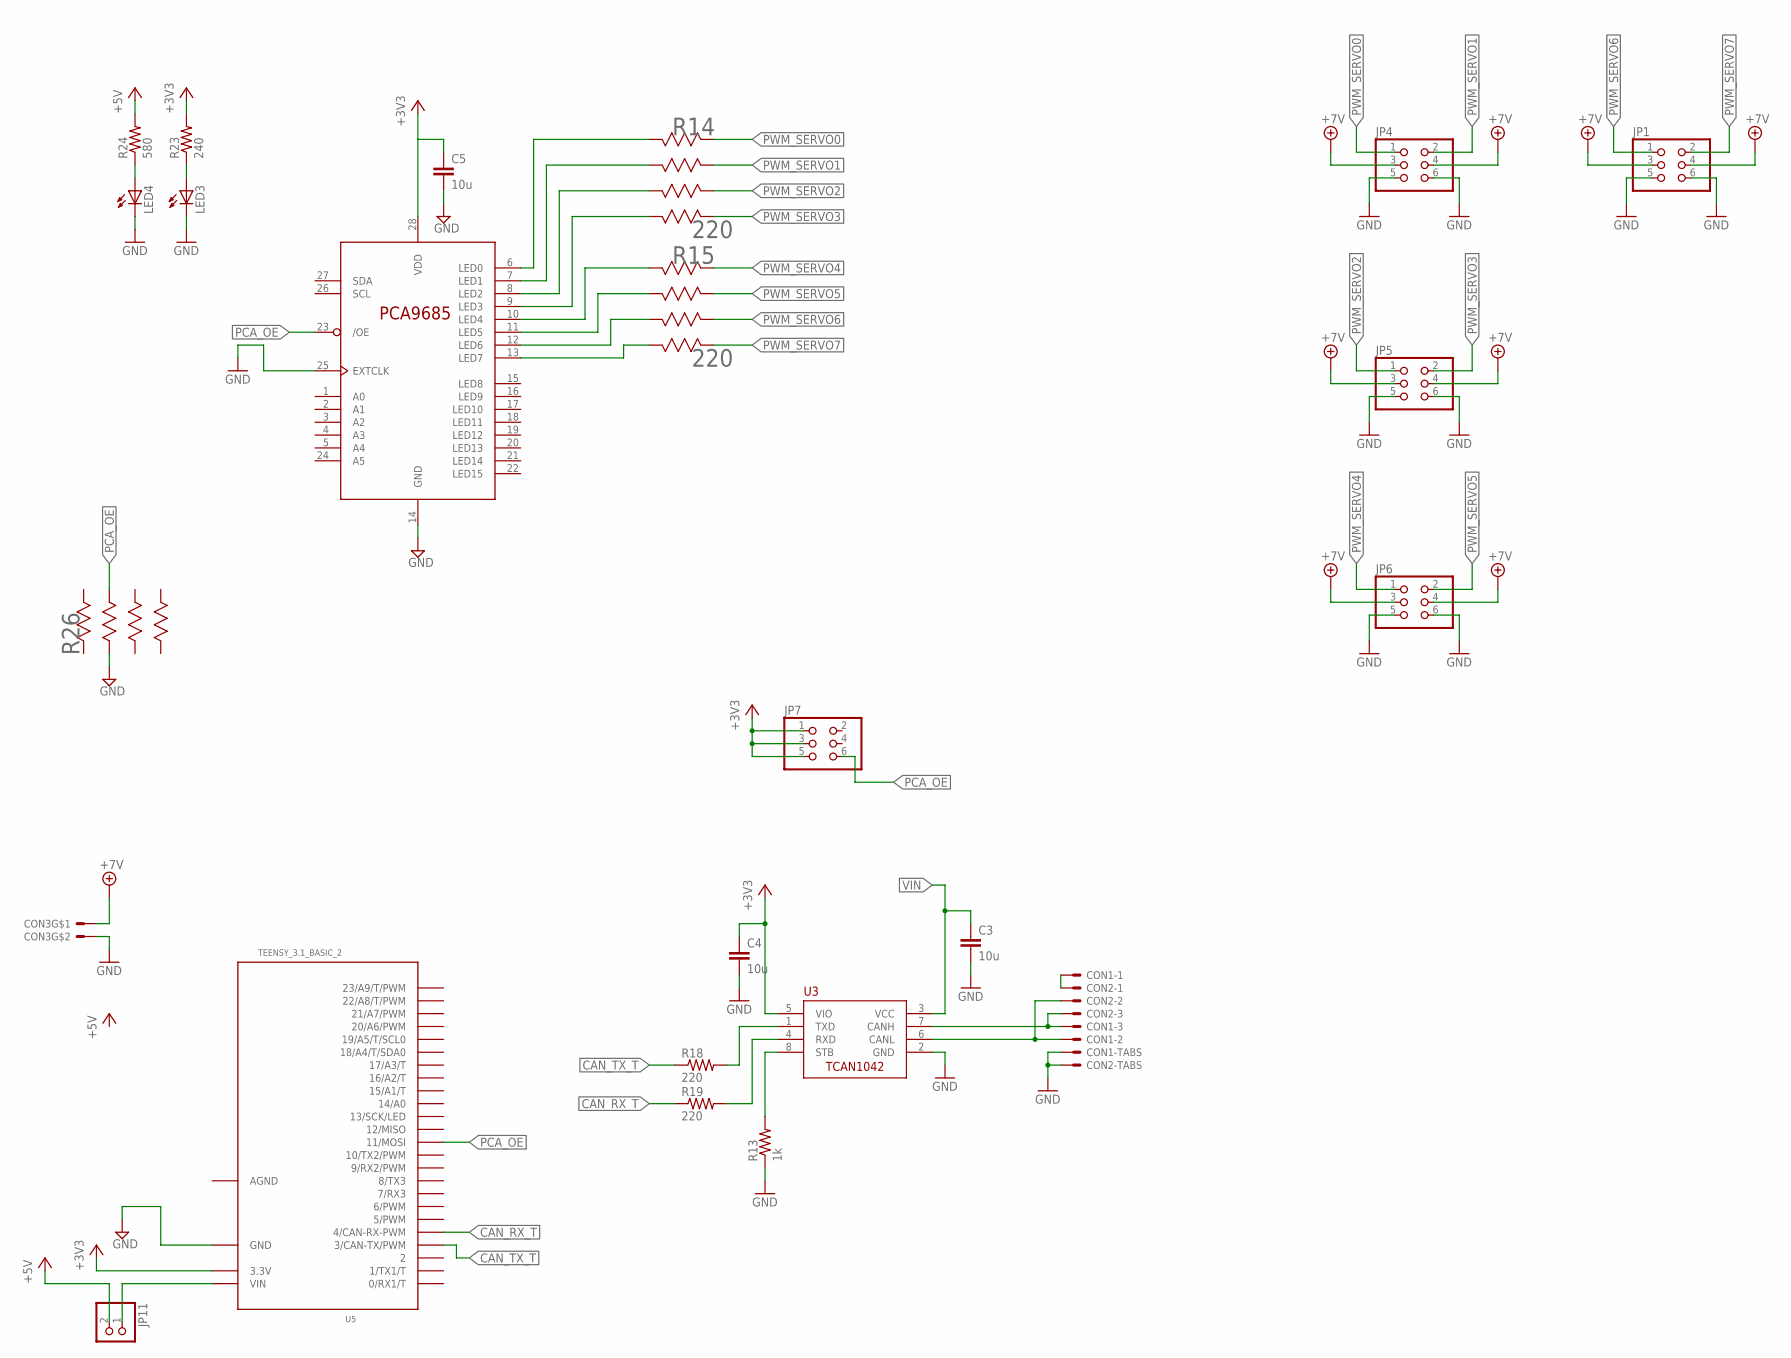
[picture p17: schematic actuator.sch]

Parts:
C3, C4, C5: 10u; C0805
CON1, CON2: SM03B-GHS-TB
CON3: MOLEX_5566-2; 5566-2
JP1, JP4, JP5, JP6, JP7: PINHD-2X3; 2X03
JP11: PINHD-1X2; 1X02
LED3, LED4: LEDCHIPLED_1206; CHIPLED_1206
R13: 1k; R0805
R14, R15: 220; EXBV8V-M
R18, R19: 220; R0805
R23: 240; R1206
R24: 580; R1206
R26: 10k; EXBV8V-M
U3: TCAN1042HVDR; SO-8
U4: PCA9685PW; TSSOP28
U5: TEENSY_3.1_BASIC_2

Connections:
+3V3: C4.1, C5.1, JP7.1, JP7.3, JP7.5, R23.2, U3.5 (VIO), U4.28 (VDD), U5.3.3V
+5V: JP11.2, R24.2
+7V: CON3.1, JP1.3, JP1.4, JP4.3, JP4.4, JP5.3, JP5.4, JP6.3, JP6.4
AGND: U5.AGND
CANH: CON1.P$3, CON2.P$3, U3.7 (CANH)
CANL: CON1.P$2, CON2.P$2, U3.6 (CANL)
CANSH: CON1.P$1, CON2.P$1
CAN_RX: R19.2, U3.4 (RXD)
CAN_RX_T: R19.1, U5.4 (4/CAN-RX-PWM)
CAN_TX1: R18.2, U3.1 (TXD)
CAN_TX_T: R18.1, U5.3 (3/CAN-TX/PWM)
GND: C3.2, C4.2, C5.2, CON1.P$4, CON1.P$5, CON2.P$4, CON2.P$5, CON3.2, JP1.5, JP1.6, JP4.5, JP4.6, JP5.5, JP5.6, JP6.5, JP6.6, LED3.C, LED4.C, R13.1, R26.2 (23), U3.2 (GND), U4.14 (GND), U4.25 (EXTCLK), U5.GND
unnamed: LED3.A, R23.1
unnamed: LED4.A, R24.1
PCA_OE: JP7.6, R26.7 (74), U4.23 (/OE), U5.11 (11/MOSI)
PWM_CH0: R14.8 (82), U4.6 (LED0)
PWM_CH1: R14.7 (74), U4.7 (LED1)
PWM_CH2: R14.6 (66), U4.8 (LED2)
PWM_CH3: R14.5 (58), U4.9 (LED3)
PWM_CH4: R15.8 (82), U4.10 (LED4)
PWM_CH5: R15.7 (74), U4.11 (LED5)
PWM_CH6: R15.6 (66), U4.12 (LED6)
PWM_CH7: R15.5 (58), U4.13 (LED7)
PWM_SERVO0: JP4.1, R14.1 (11)
PWM_SERVO1: JP4.2, R14.2 (23)
PWM_SERVO2: JP5.1, R14.3 (35)
PWM_SERVO3: JP5.2, R14.4 (47)
PWM_SERVO4: JP6.1, R15.1 (11)
PWM_SERVO5: JP6.2, R15.2 (23)
PWM_SERVO6: JP1.1, R15.3 (35)
PWM_SERVO7: JP1.2, R15.4 (47)
STB: R13.2, U3.8 (STB)
VIN: C3.1, JP11.1, U3.3 (VCC), U5.VIN

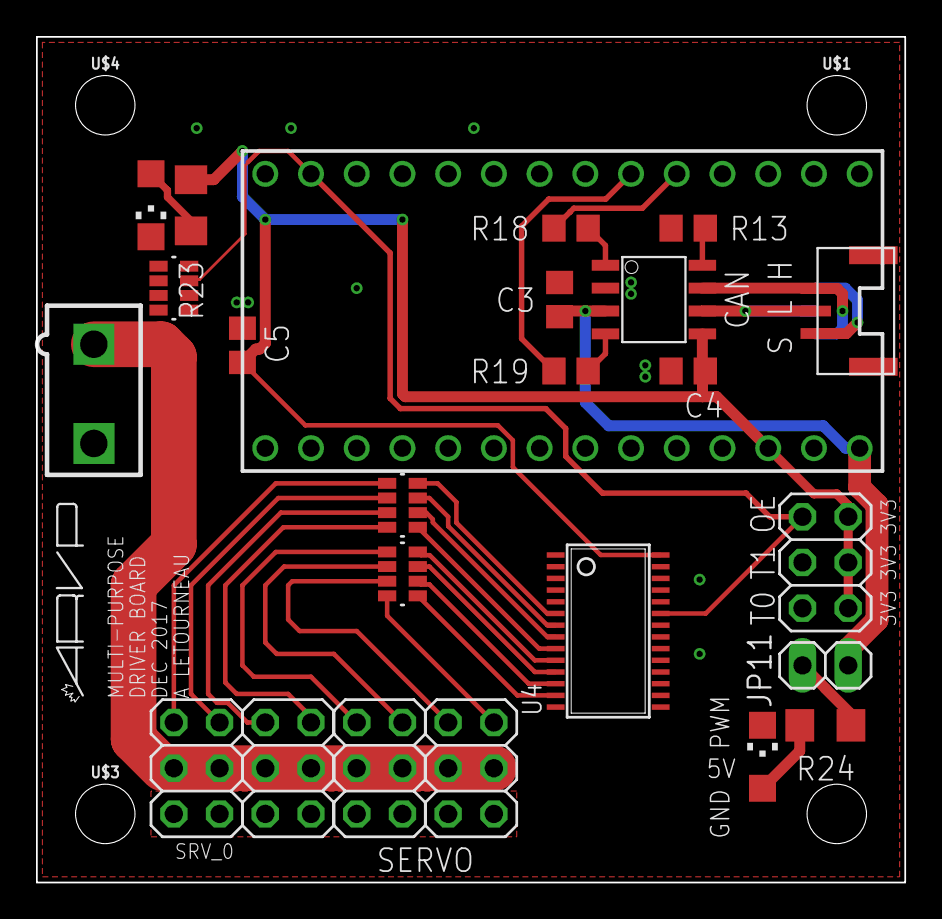
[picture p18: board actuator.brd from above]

Board: 2 copper layers, 48.3 x 47.0 mm, 32 parts (1 on the bottom side), 32 nets.

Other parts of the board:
U$1, U$3, U$4, U$8: STAND-OFF
U$5: LOGO3
U$6: LETTER_L
U$7: DOCFIELD

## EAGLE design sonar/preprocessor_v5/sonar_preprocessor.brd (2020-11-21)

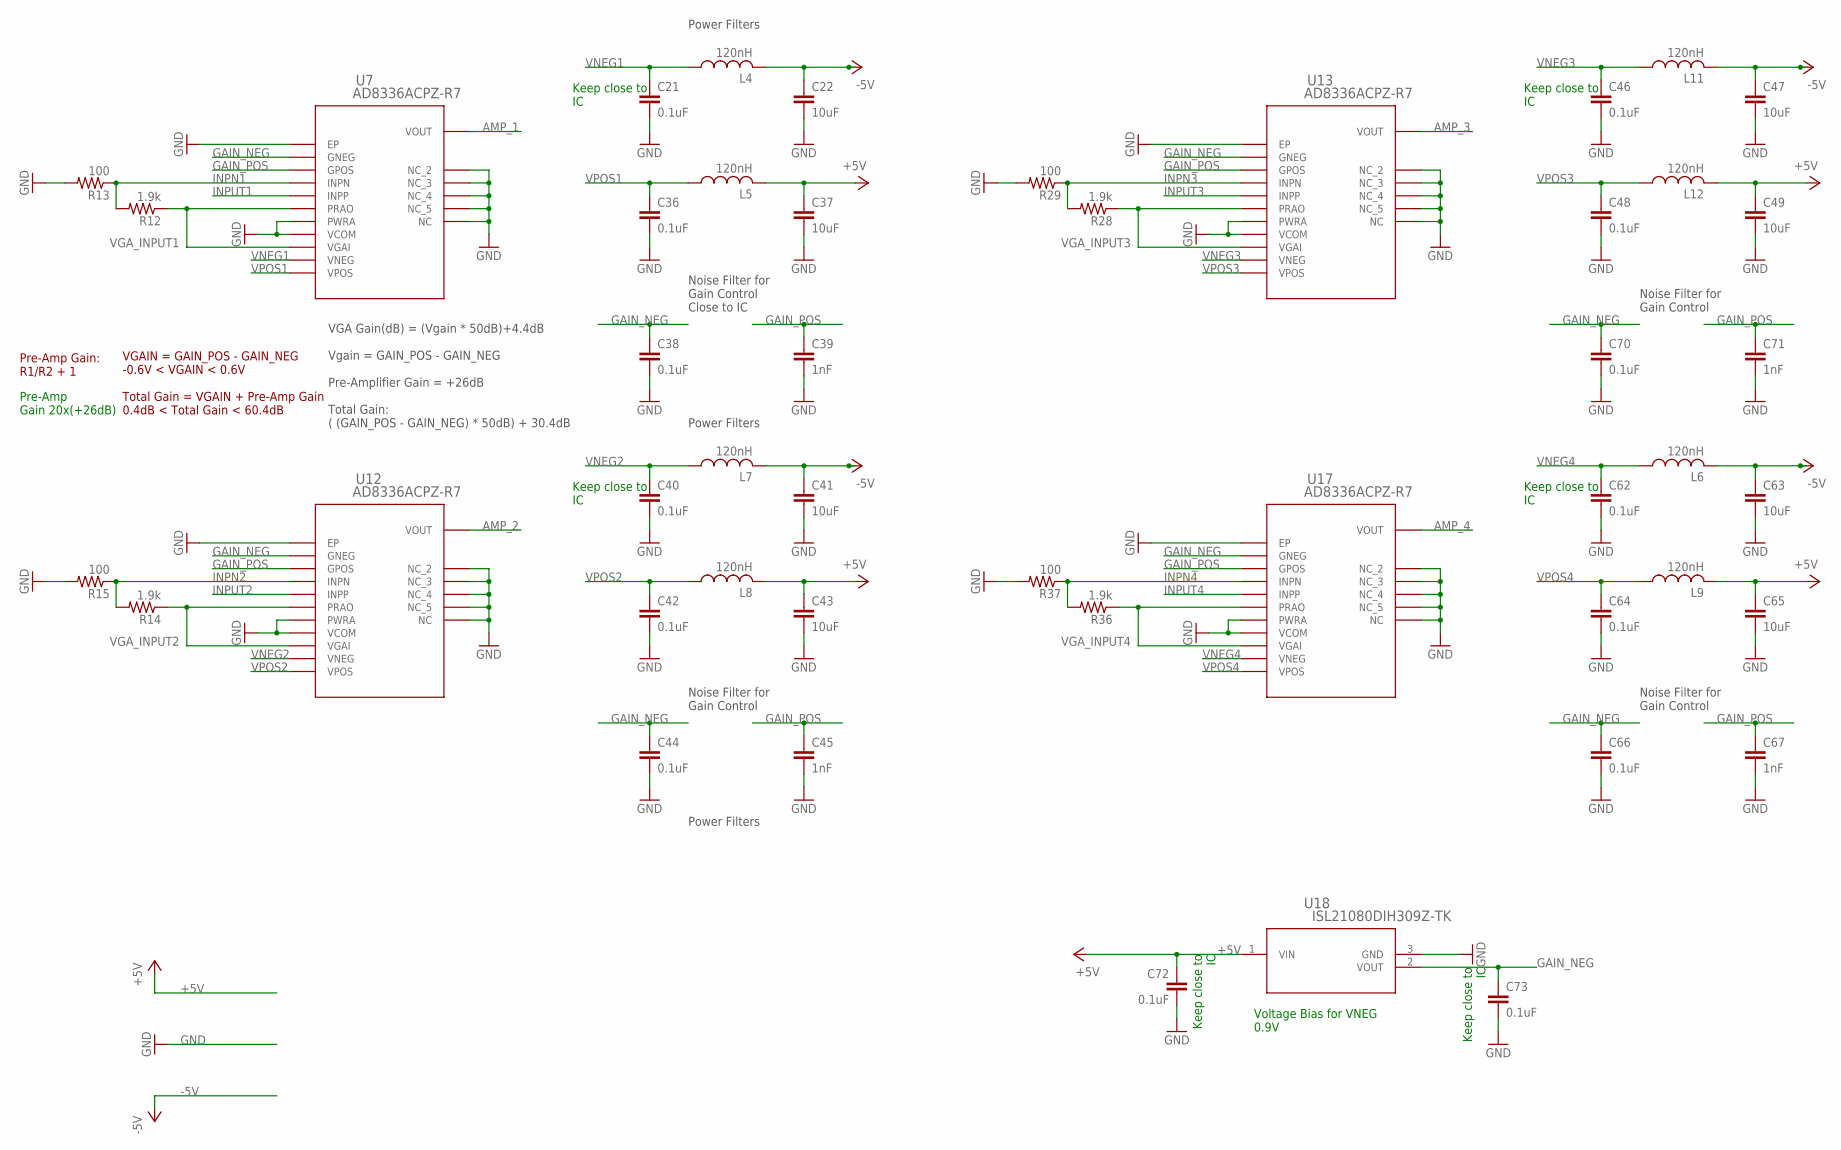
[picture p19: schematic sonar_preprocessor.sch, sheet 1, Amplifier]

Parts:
C21, C36, C38, C40, C42, C44, C46, C48, C62, C64, C66, C70, C72, C73: 0.1uF; C0603
C22, C37, C41, C43, C47, C49, C63, C65: 10uF; C1206
C39, C45, C67, C71: 1nF; C0603
L4, L5, L6, L7, L8, L9, L11, L12: 120nH; L3225P
R12, R14, R28, R36: 1.9k; R0603
R13, R15, R29, R37: 100; R0603
U7, U12, U13, U17: AD8336ACPZ-R7; CP_16_4
U18: ISL21080DIH309Z-TK; P3_064

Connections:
+5V: C37.1, C43.1, C49.1, C65.1, C72.1, L5.2, L8.2, L9.2, L12.2, U18.1 (VIN); also elsewhere on the board
-5V: C22.1, C41.1, C47.1, C63.1, L4.2, L6.2, L7.2, L11.2; also elsewhere on the board
AMP_1: U7.VOUT; also elsewhere on the board
AMP_2: U12.VOUT; also elsewhere on the board
AMP_3: U13.VOUT; also elsewhere on the board
AMP_4: U17.VOUT; also elsewhere on the board
GAIN_NEG: C38.1, C44.1, C66.1, C70.1, C73.1, U7.GNEG, U12.GNEG, U13.GNEG, U17.GNEG, U18.2 (VOUT)
GAIN_POS: C39.1, C45.1, C67.1, C71.1, U7.GPOS, U12.GPOS, U13.GPOS, U17.GPOS; also elsewhere on the board
GND: C21.2, C22.2, C36.2, C37.2, C38.2, C39.2, C40.2, C41.2, C42.2, C43.2, C44.2, C45.2, C46.2, C47.2, C48.2, C49.2, C62.2, C63.2, C64.2, C65.2, C66.2, C67.2, C70.2, C71.2, C72.2, C73.2, R13.2, R15.2, R29.2, R37.2, U7.GND1 (EP), U7.NC, U7.NC1 (NC_2), U7.NC2 (NC_3), U7.NC3 (NC_4), U7.NC4 (NC_5), U7.PWRA, U7.VCOM, U12.GND1 (EP), U12.NC, U12.NC1 (NC_2), U12.NC2 (NC_3), U12.NC3 (NC_4), U12.NC4 (NC_5), U12.PWRA, U12.VCOM, U13.GND1 (EP), U13.NC, U13.NC1 (NC_2), U13.NC2 (NC_3), U13.NC3 (NC_4), U13.NC4 (NC_5), U13.PWRA, U13.VCOM, U17.GND1 (EP), U17.NC, U17.NC1 (NC_2), U17.NC2 (NC_3), U17.NC3 (NC_4), U17.NC4 (NC_5), U17.PWRA, U17.VCOM, U18.3 (GND); also elsewhere on the board
INPN1: R12.2, R13.1, U7.INPN
INPN2: R14.2, R15.1, U12.INPN
INPN3: R28.2, R29.1, U13.INPN
INPN4: R36.2, R37.1, U17.INPN
INPUT1: U7.INPP; also elsewhere on the board
INPUT2: U12.INPP; also elsewhere on the board
INPUT3: U13.INPP; also elsewhere on the board
INPUT4: U17.INPP; also elsewhere on the board
VGA_INPUT1: R12.1, U7.PRAO, U7.VGAI
VGA_INPUT2: R14.1, U12.PRAO, U12.VGAI
VGA_INPUT3: R28.1, U13.PRAO, U13.VGAI
VGA_INPUT4: R36.1, U17.PRAO, U17.VGAI
VNEG1: C21.1, L4.1, U7.VNEG
VNEG2: C40.1, L7.1, U12.VNEG
VNEG3: C46.1, L11.1, U13.VNEG
VNEG4: C62.1, L6.1, U17.VNEG
VPOS1: C36.1, L5.1, U7.VPOS
VPOS2: C42.1, L8.1, U12.VPOS
VPOS3: C48.1, L12.1, U13.VPOS
VPOS4: C64.1, L9.1, U17.VPOS

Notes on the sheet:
Pre-Amp Gain 20x(+26dB)
Power Filters
Keep close to IC
Noise Filter for Gain Control Close to IC
Pre-Amp Gain: R1/R2 + 1
VGA Gain(dB) = (Vgain * 50dB)+4.4dB Vgain = GAIN_POS - GAIN_NEG Pre-Amplifier Gain = +26dB Total Gain: ( (GAIN_POS - GAIN_NEG) * 50dB) + 30.4dB
VGAIN = GAIN_POS - GAIN_NEG -0.6V < VGAIN < 0.6V Total Gain = VGAIN + Pre-Amp Gain 0.4dB < Total Gain < 60.4dB
Noise Filter for Gain Control
Voltage Bias for VNEG 0.9V

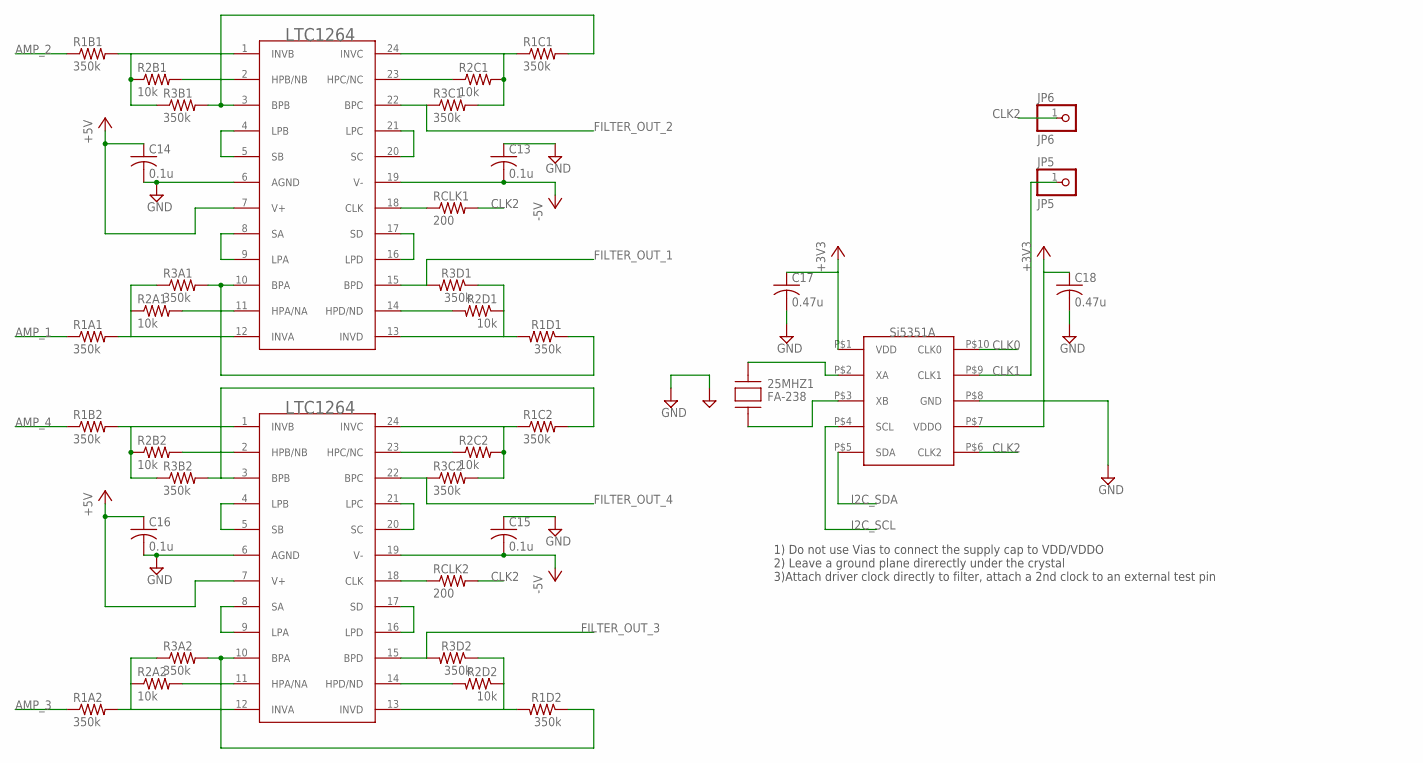
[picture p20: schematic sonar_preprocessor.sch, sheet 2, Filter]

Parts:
25MHZ1: FA-238
C13, C14, C15, C16: 0.1u; C0805
C17, C18: 0.47u; C0805
JP5: JP5; 1X01
JP6: JP6; 1X01
R1A1, R1A2, R1B1, R1B2, R1C1, R1C2, R1D1, R1D2, R3A1, R3A2, R3B1, R3B2, R3C1, R3C2, R3D1, R3D2: 350k; R0805
R2A1, R2A2, R2B1, R2B2, R2C1, R2C2, R2D1, R2D2: 10k; R0805
RCLK1, RCLK2: 200; R0805
U$6, U$7: LTC1264SMD; SO24W
U$8: SI5351A; MSOP-10

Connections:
+3V3: C17.1, C18.1, U$8.P$1 (VDD), U$8.P$7 (VDDO); also elsewhere on the board
+5V: C14.1, C16.1, U$6.7 (V+), U$7.7 (V+); also elsewhere on the board
-5V: C13.2, C15.2, U$6.19 (V-), U$7.19 (V-); also elsewhere on the board
AMP_1: R1A1.1; also elsewhere on the board
AMP_2: R1B1.1; also elsewhere on the board
AMP_3: R1A2.1; also elsewhere on the board
AMP_4: R1B2.1; also elsewhere on the board
CLK0: U$8.P$10 (CLK0)
CLK1: JP5.1, U$8.P$9 (CLK1)
CLK2: JP6.1, RCLK1.2, RCLK2.2, U$8.P$6 (CLK2)
FILTER_OUT_1: R3D1.2, U$6.15 (BPD); also elsewhere on the board
FILTER_OUT_2: R3C1.1, U$6.22 (BPC); also elsewhere on the board
FILTER_OUT_3: R3D2.2, U$7.15 (BPD); also elsewhere on the board
FILTER_OUT_4: R3C2.1, U$7.22 (BPC); also elsewhere on the board
GND: 25MHZ1.P$1 (GND), 25MHZ1.P$3 (GND), C13.1, C14.2, C15.1, C16.2, C17.2, C18.2, U$6.6 (AGND), U$7.6 (AGND), U$8.P$8 (GND); also elsewhere on the board
I2C_SCL: U$8.P$4 (SCL); also elsewhere on the board
I2C_SDA: U$8.P$5 (SDA); also elsewhere on the board
unnamed: U$7.20 (SC), U$7.21 (LPC)
unnamed: 25MHZ1.P$4 (XA), U$8.P$2 (XA)
unnamed: 25MHZ1.P$2 (XB), U$8.P$3 (XB)
unnamed: R2A1.2, U$6.11 (HPA/NA)
unnamed: U$6.8 (SA), U$6.9 (LPA)
unnamed: R1A1.2, R2A1.1, R3A1.1, U$6.12 (INVA)
unnamed: R2D1.2, U$6.14 (HPD/ND)
unnamed: R1D1.2, R2D1.1, R3D1.1, U$6.13 (INVD)
unnamed: U$6.16 (LPD), U$6.17 (SD)
unnamed: R2C1.1, U$6.23 (HPC/NC)
unnamed: R1C1.1, R2C1.2, R3C1.2, U$6.24 (INVC)
unnamed: R2C2.1, U$7.23 (HPC/NC)
unnamed: R2B1.2, U$6.2 (HPB/NB)
unnamed: R1B1.2, R2B1.1, R3B1.1, U$6.1 (INVB)
unnamed: U$6.4 (LPB), U$6.5 (SB)
unnamed: U$6.20 (SC), U$6.21 (LPC)
unnamed: RCLK1.1, U$6.18 (CLK)
unnamed: R2A2.2, U$7.11 (HPA/NA)
unnamed: U$7.8 (SA), U$7.9 (LPA)
unnamed: R1A2.2, R2A2.1, R3A2.1, U$7.12 (INVA)
unnamed: R2D2.2, U$7.14 (HPD/ND)
unnamed: R1D2.2, R2D2.1, R3D2.1, U$7.13 (INVD)
unnamed: U$7.16 (LPD), U$7.17 (SD)
unnamed: R1C2.1, R2C2.2, R3C2.2, U$7.24 (INVC)
unnamed: R2B2.2, U$7.2 (HPB/NB)
unnamed: R1B2.2, R2B2.1, R3B2.1, U$7.1 (INVB)
unnamed: U$7.4 (LPB), U$7.5 (SB)
unnamed: RCLK2.1, U$7.18 (CLK)
OUT_2ND_A1: R1D1.1, R3A1.2, U$6.10 (BPA)
OUT_2ND_A2: R1D2.1, R3A2.2, U$7.10 (BPA)
OUT_2ND_B2: R1C2.2, R3B2.2, U$7.3 (BPB)
OUT_2ND_ORDER_B1: R1C1.2, R3B1.2, U$6.3 (BPB)

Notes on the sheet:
1) Do not use Vias to connect the supply cap to VDD/VDDO 2) Leave a ground plane direrectly under the crystal 3)Attach driver clock directly to filter, attach a 2nd clock to an external test pin

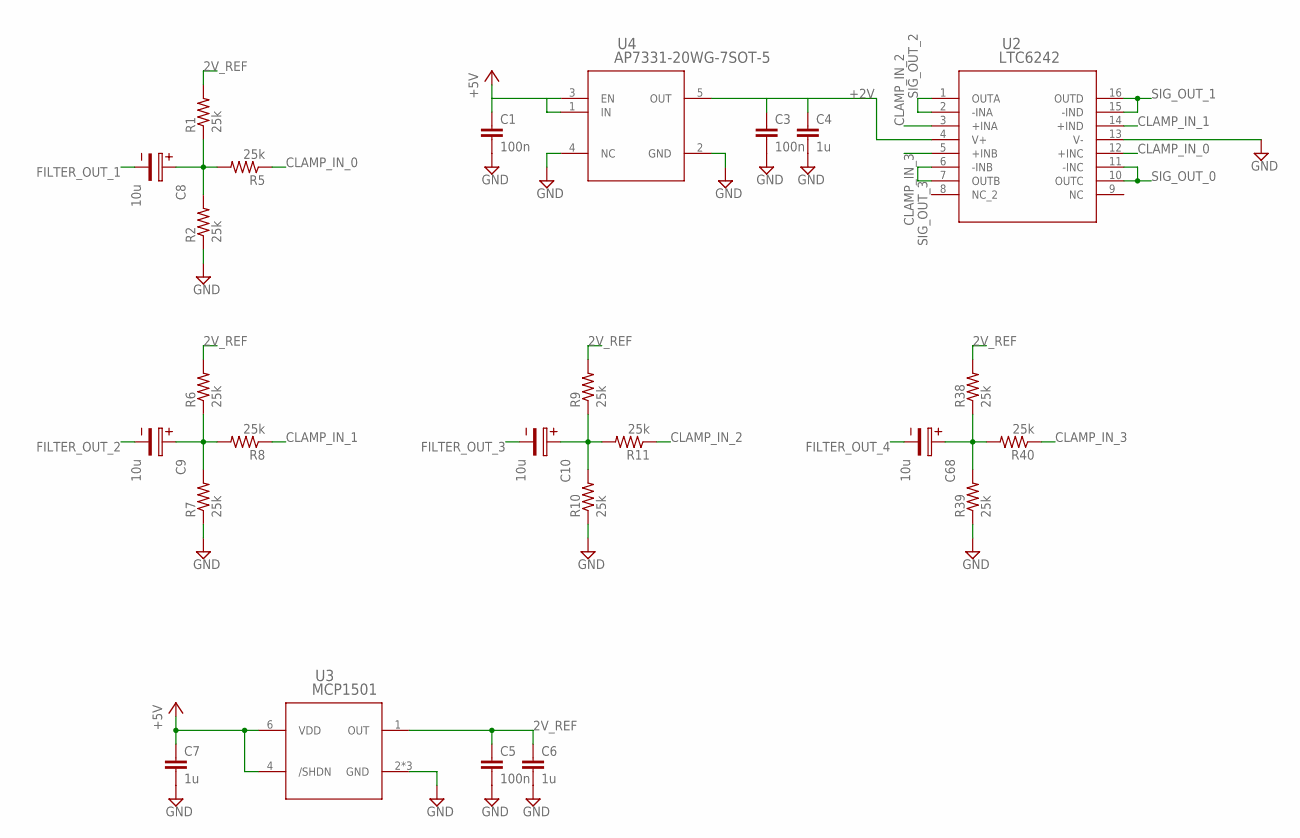
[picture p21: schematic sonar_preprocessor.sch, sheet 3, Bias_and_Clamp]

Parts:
C1, C3, C5: 100n; C0805
C4, C6, C7: 1u; C0805
C8, C9, C10, C68: 10u; 2.6X1.6X1(BXCXA)
R1, R2, R5, R6, R7, R8, R9, R10, R11, R38, R39, R40: 25k; R0805
U2: LTC6242; SSOP16
U3: MCP1501; SOT23-6
U4: AP7331-20WG-7SOT-5; SOT23-5

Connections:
2V_REF: C5.1, C6.1, R1.2, R6.2, R9.2, R38.2, U3.1 (OUT)
+2V: C3.1, C4.1, U2.4 (V+), U4.5 (OUT)
+5V: C1.1, C7.1, U3.4 (/SHDN), U3.6 (VDD), U4.1 (IN), U4.3 (EN); also elsewhere on the board
BIASED_0: C8.1, R1.1, R2.2, R5.2
BIASED_1: C9.1, R6.1, R7.2, R8.2
BIASED_2: C10.1, R9.1, R10.2, R11.2
BIASED_3: C68.1, R38.1, R39.2, R40.2
CLAMP_IN_0: R5.1, U2.12 (+INC)
CLAMP_IN_1: R8.1, U2.14 (+IND)
CLAMP_IN_2: R11.1, U2.3 (+INA)
CLAMP_IN_3: R40.1, U2.5 (+INB)
FILTER_OUT_1: C8.2; also elsewhere on the board
FILTER_OUT_2: C9.2; also elsewhere on the board
FILTER_OUT_3: C10.2; also elsewhere on the board
FILTER_OUT_4: C68.2; also elsewhere on the board
GND: C1.2, C3.2, C4.2, C5.2, C6.2, C7.2, R2.1, R7.1, R10.1, R39.1, U2.13 (V-), U3.2 (GND), U3.3 (GND), U3.5 (GND), U4.2 (GND), U4.4 (NC); also elsewhere on the board
SIG_OUT_0: U2.10 (OUTC), U2.11 (-INC); also elsewhere on the board
SIG_OUT_1: U2.15 (-IND), U2.16 (OUTD); also elsewhere on the board
SIG_OUT_2: U2.1 (OUTA), U2.2 (-INA); also elsewhere on the board
SIG_OUT_3: U2.6 (-INB), U2.7 (OUTB); also elsewhere on the board

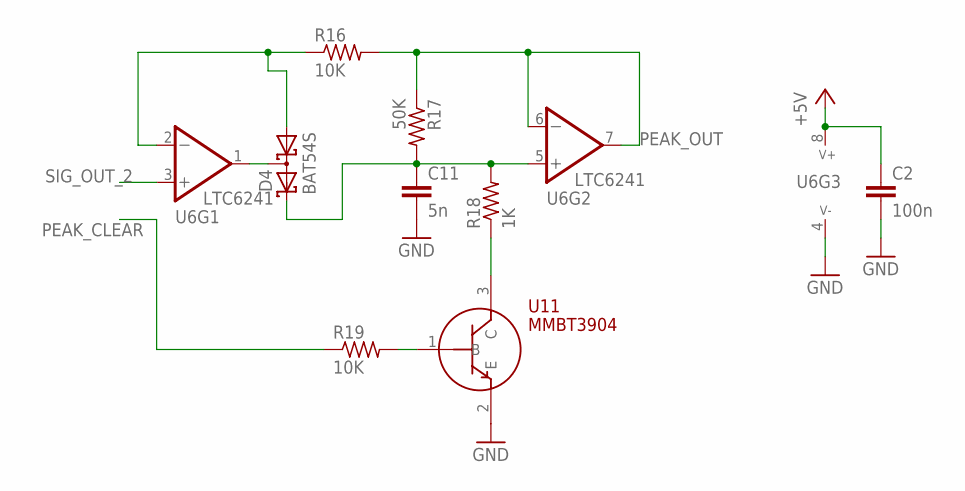
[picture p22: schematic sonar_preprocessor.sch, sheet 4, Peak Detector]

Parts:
C2: 100n; C0805
C11: 5n; C0805
D4: BAT54S; SOT23
R16, R19: 10K; R0805
R17: 50K; R0805
R18: 1K; R0805
U6: LTC6241; SO-8
U11: MMBT3904; SOT23

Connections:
+5V: C2.1, U6.8 (V+); also elsewhere on the board
GND: C2.2, C11.2, U6.4 (V-), U11.2 (E); also elsewhere on the board
unnamed: C11.1, D4.2 (C2), R17.2, R18.2, U6.5 (+IN)
unnamed: D4.1 (A1), R16.1, U6.2 (-IN)
unnamed: D4.3 (C1A2), U6.1 (OUT)
unnamed: R19.2, U11.1 (B)
unnamed: R18.1, U11.3 (C)
PEAK_CLEAR: R19.1; also elsewhere on the board
PEAK_OUT: R16.2, R17.1, U6.6 (-IN), U6.7 (OUT); also elsewhere on the board
SIG_OUT_2: U6.3 (+IN); also elsewhere on the board

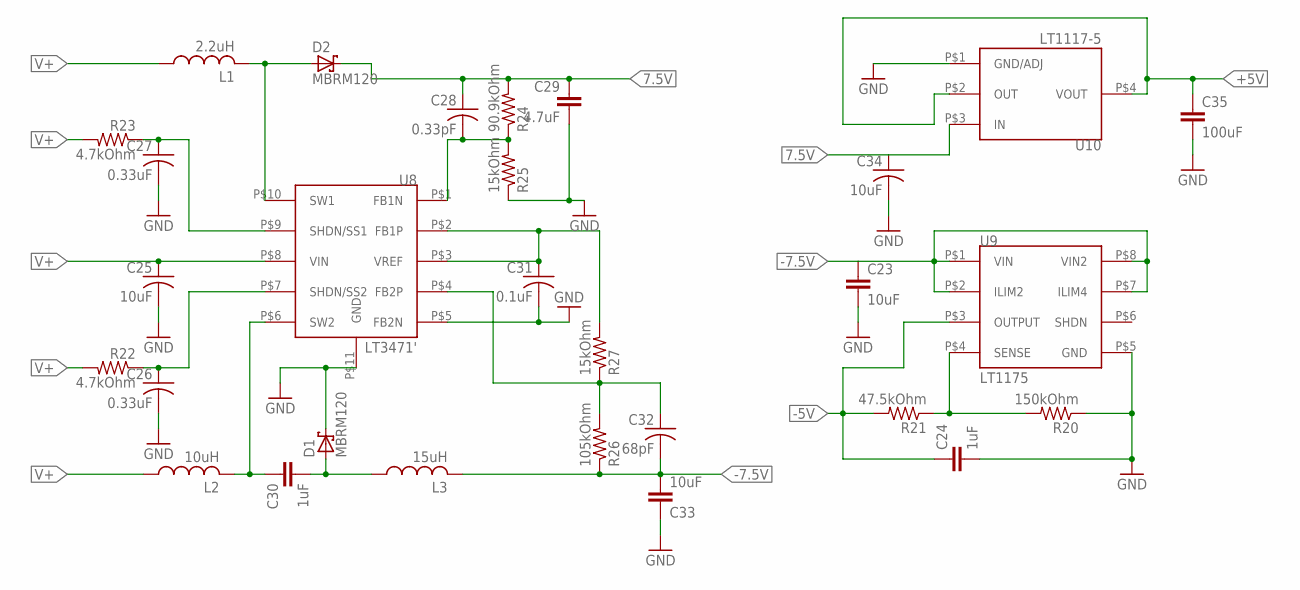
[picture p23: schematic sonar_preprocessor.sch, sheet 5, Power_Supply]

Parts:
C23, C33: 10uF; C0805
C24, C30: 1uF; C1206
C25, C34: 10uF; C0603
C26, C27: 0.33uF; C0603
C28: 0.33pF; C0603
C29: 4.7uF; C1206
C31: 0.1uF; C0603
C32: 68pF; C0603
C35: 100uF; C1210
D1, D2: MBRM120; DO-216AA
L1: 2.2uH; NS4.9X4.9
L2: 10uH; NS5X5
L3: 15uH; NS5X5
R20: 150kOhm; R0603
R21: 47.5kOhm; R0603
R22, R23: 4.7kOhm; R0603
R24: 90.9kOhm; R0603
R25, R27: 15kOhm; R0603
R26: 105kOhm; R0603
U8: LT3471'; 10-WFDFN
U9: LT1175; 8-SOIC
U10: LT1117-5; SOT233-3

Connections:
7.5V: C28.1, C29.1, C34.1, D2.P$1 (C), R24.2, U10.P$3 (IN)
+5V: C35.1, U10.P$2 (OUT), U10.P$4 (VOUT); also elsewhere on the board
-5V: C24.1, R21.2, U9.P$3 (OUTPUT); also elsewhere on the board
-7.5V: C23.1, C32.2, C33.2, L3.P$2 (2), R26.1, U9.P$1 (VIN), U9.P$2 (ILIM2), U9.P$7 (ILIM4), U9.P$8 (VIN2)
GND: C23.2, C24.2, C25.2, C26.2, C27.2, C29.2, C31.2, C33.1, C34.2, C35.2, D1.P$1 (C), R20.1, R25.1, U8.P$5 (FB2N), U8.P$11 (GND), U9.P$5 (GND), U10.P$1 (GND/ADJ); also elsewhere on the board
unnamed: R20.2, R21.1, U9.P$4 (SENSE)
unnamed: D2.P$2 (A), L1.P$2 (2), U8.P$10 (SW1)
unnamed: C28.2, R24.1, R25.2, U8.P$1 (FB1N)
unnamed: C30.1, L2.P$2 (2), U8.P$6 (SW2)
unnamed: C30.2, D1.P$2 (A), L3.P$1 (1)
unnamed: C32.1, R26.2, R27.1, U8.P$4 (FB2P)
SS3: C26.1, R22.1, U8.P$7 (SHDN/SS2)
SS4: C27.1, R23.1, U8.P$9 (SHDN/SS1)
V+: C25.1, L1.P$1 (1), L2.P$1 (1), R22.2, R23.2, U8.P$8 (VIN); also elsewhere on the board
VREF: C31.1, R27.2, U8.P$2 (FB1P), U8.P$3 (VREF)

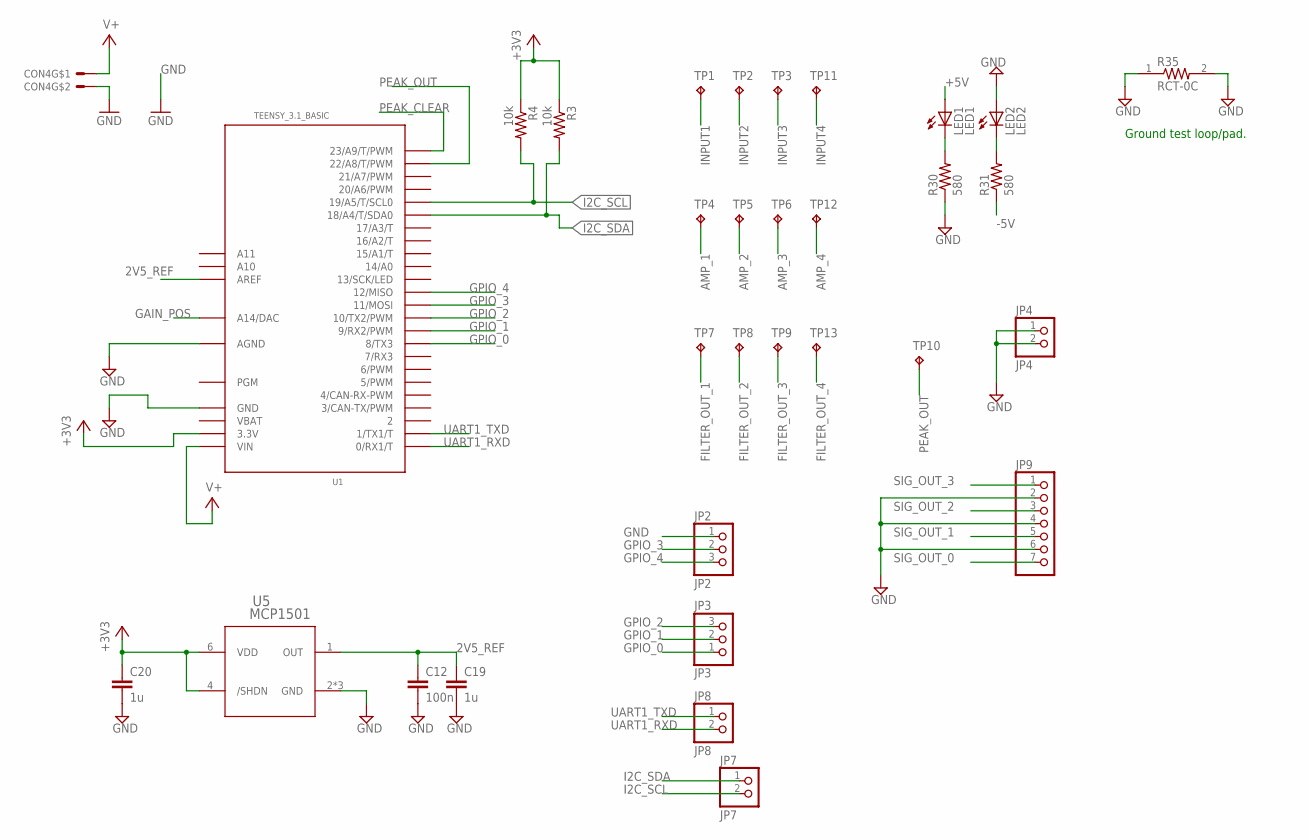
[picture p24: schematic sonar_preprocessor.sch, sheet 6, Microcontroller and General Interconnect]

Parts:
C12: 100n; C0805
C19, C20: 1u; C0805
CON4: MOLEX_5566-2; 5566-2
JP2: JP2; 1X03SMD/90
JP3: JP3; 1X03SMD/90
JP4: JP4; 1X02
JP7: JP7; 1X02
JP8: JP8; 1X02SMD/90
JP9: PINHD-1X7/90; 1X07/90
LED1: LED1; SML0805
LED2: LED2; SML0805
R3, R4: 10k; R0805
R30, R31: 580; R0805
R35: RCT-0C; RESC2012X65N
TP1, TP2, TP3, TP4, TP5, TP6, TP7, TP8, TP9, TP10, TP11, TP12, TP13: TPB2,54; B2,54
U1: TEENSY_3.1_BASIC
U5: MCP1501; SOT23-6

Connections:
2V5_REF: C12.1, C19.1, U1.AREF, U5.1 (OUT)
+3V3: C20.1, R3.1, R4.1, U1.3.3V, U1.3.3V1 (3.3V), U5.4 (/SHDN), U5.6 (VDD); also elsewhere on the board
+5V: LED1.A; also elsewhere on the board
-5V: R31.1; also elsewhere on the board
AMP_1: TP4.TP; also elsewhere on the board
AMP_2: TP5.TP; also elsewhere on the board
AMP_3: TP6.TP; also elsewhere on the board
AMP_4: TP12.TP; also elsewhere on the board
FILTER_OUT_1: TP7.TP; also elsewhere on the board
FILTER_OUT_2: TP8.TP; also elsewhere on the board
FILTER_OUT_3: TP9.TP; also elsewhere on the board
FILTER_OUT_4: TP13.TP; also elsewhere on the board
GAIN_POS: U1.A14 (A14/DAC); also elsewhere on the board
GND: C12.2, C19.2, C20.2, CON4.2, JP2.1, JP4.1, JP4.2, JP9.2, JP9.4, JP9.6, LED2.A, R30.1, R35.1, R35.2, U1.AGND, U1.GND, U1.GND1 (GND), U5.2 (GND), U5.3 (GND), U5.5 (GND); also elsewhere on the board
GPIO_0: JP3.1, U1.8 (8/TX3)
GPIO_1: JP3.2, U1.9 (9/RX2/PWM)
GPIO_2: JP3.3, U1.10 (10/TX2/PWM)
GPIO_3: JP2.2, U1.11 (11/MOSI)
GPIO_4: JP2.3, U1.12 (12/MISO)
I2C_SCL: JP7.2, R4.2, U1.19/A5 (19/A5/T/SCL0); also elsewhere on the board
I2C_SDA: JP7.1, R3.2, U1.18/A4 (18/A4/T/SDA0); also elsewhere on the board
INPUT1: TP1.TP; also elsewhere on the board
INPUT2: TP2.TP; also elsewhere on the board
INPUT3: TP3.TP; also elsewhere on the board
INPUT4: TP11.TP; also elsewhere on the board
unnamed: LED2.C, R31.2
unnamed: LED1.C, R30.2
PEAK_CLEAR: U1.23/A9 (23/A9/T/PWM); also elsewhere on the board
PEAK_OUT: TP10.TP, U1.22/A8 (22/A8/T/PWM); also elsewhere on the board
SIG_OUT_0: JP9.7; also elsewhere on the board
SIG_OUT_1: JP9.5; also elsewhere on the board
SIG_OUT_2: JP9.3; also elsewhere on the board
SIG_OUT_3: JP9.1; also elsewhere on the board
UART1_RXD: JP8.2, U1.0 (0/RX1/T)
UART1_TXD: JP8.1, U1.1 (1/TX1/T)
V+: CON4.1, U1.VIN; also elsewhere on the board
VBAT: U1.VBAT

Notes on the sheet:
Ground test loop/pad.

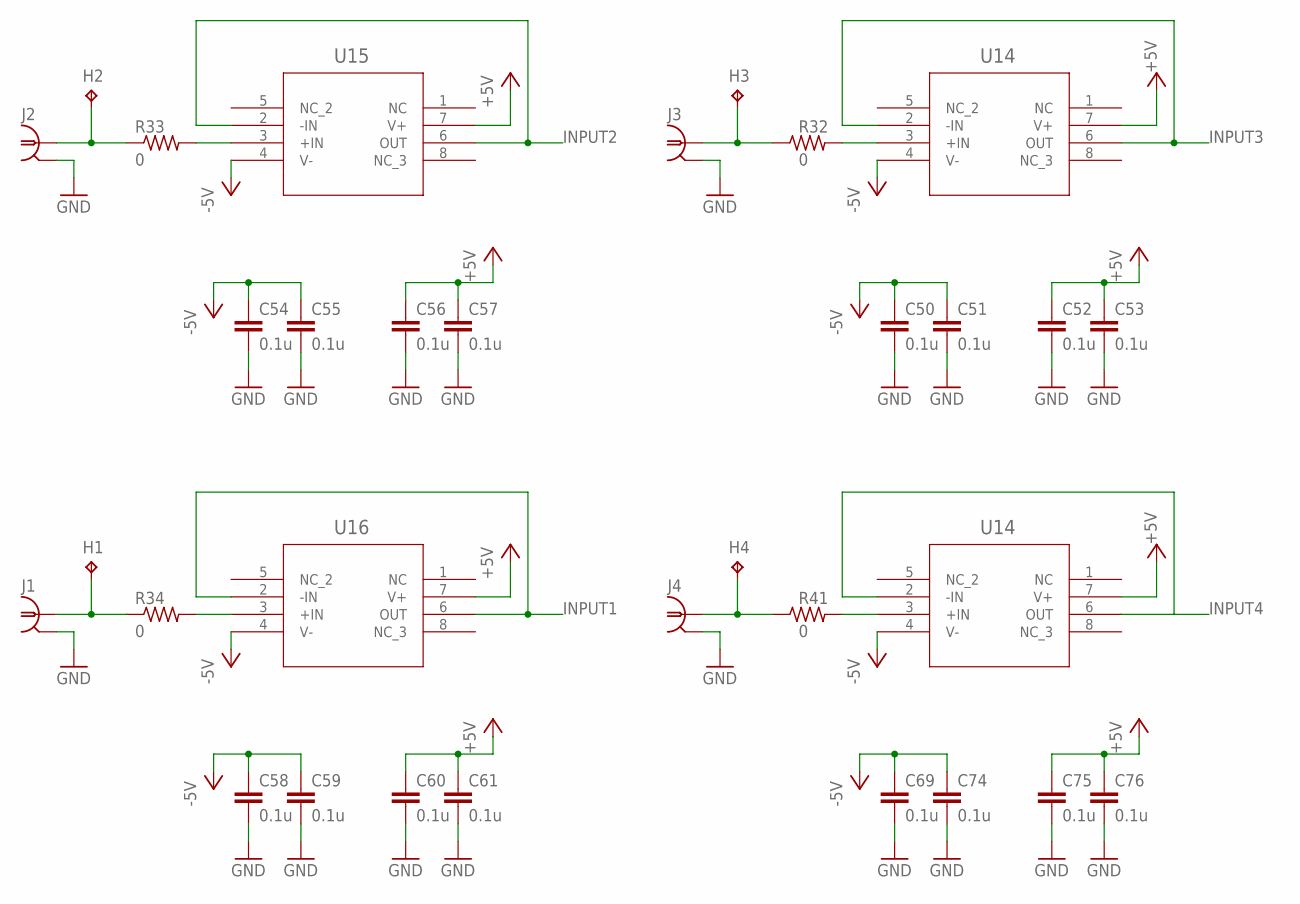
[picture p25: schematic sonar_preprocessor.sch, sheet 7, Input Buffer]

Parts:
C50, C51, C52, C53, C54, C55, C56, C57, C58, C59, C60, C61, C69, C74, C75, C76: 0.1u; C0603
H1, H2, H3, H4: TPB2,54; B2,54
J1, J2, J3, J4: TE_5-1634503-1TE; TE_5-1634503-1
R32, R33, R34, R41: 0; R0603
U14, U19: U14; SO-8
U15: U15; SO-8
U16: U16; SO-8

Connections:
+5V: C52.1, C53.1, C56.1, C57.1, C60.1, C61.1, C75.1, C76.1, U14.7 (V+), U15.7 (V+), U16.7 (V+), U19.7 (V+); also elsewhere on the board
-5V: C50.1, C51.1, C54.1, C55.1, C58.1, C59.1, C69.1, C74.1, U14.4 (V-), U15.4 (V-), U16.4 (V-), U19.4 (V-); also elsewhere on the board
GND: C50.2, C51.2, C52.2, C53.2, C54.2, C55.2, C56.2, C57.2, C58.2, C59.2, C60.2, C61.2, C69.2, C74.2, C75.2, C76.2, J1.2, J1.3 (2), J1.4 (2), J1.5 (2), J2.2, J2.3 (2), J2.4 (2), J2.5 (2), J3.2, J3.3 (2), J3.4 (2), J3.5 (2), J4.2, J4.3 (2), J4.4 (2), J4.5 (2); also elsewhere on the board
INPUT1: U16.2 (-IN), U16.6 (OUT); also elsewhere on the board
INPUT2: U15.2 (-IN), U15.6 (OUT); also elsewhere on the board
INPUT3: U14.2 (-IN), U14.6 (OUT); also elsewhere on the board
INPUT4: U19.2 (-IN), U19.6 (OUT); also elsewhere on the board
unnamed: H4.TP, J4.1, R41.1
unnamed: H3.TP, J3.1, R32.1
unnamed: R32.2, U14.3 (+IN)
unnamed: H2.TP, J2.1, R33.1
unnamed: R33.2, U15.3 (+IN)
unnamed: R34.2, U16.3 (+IN)
unnamed: H1.TP, J1.1, R34.1
unnamed: R41.2, U19.3 (+IN)

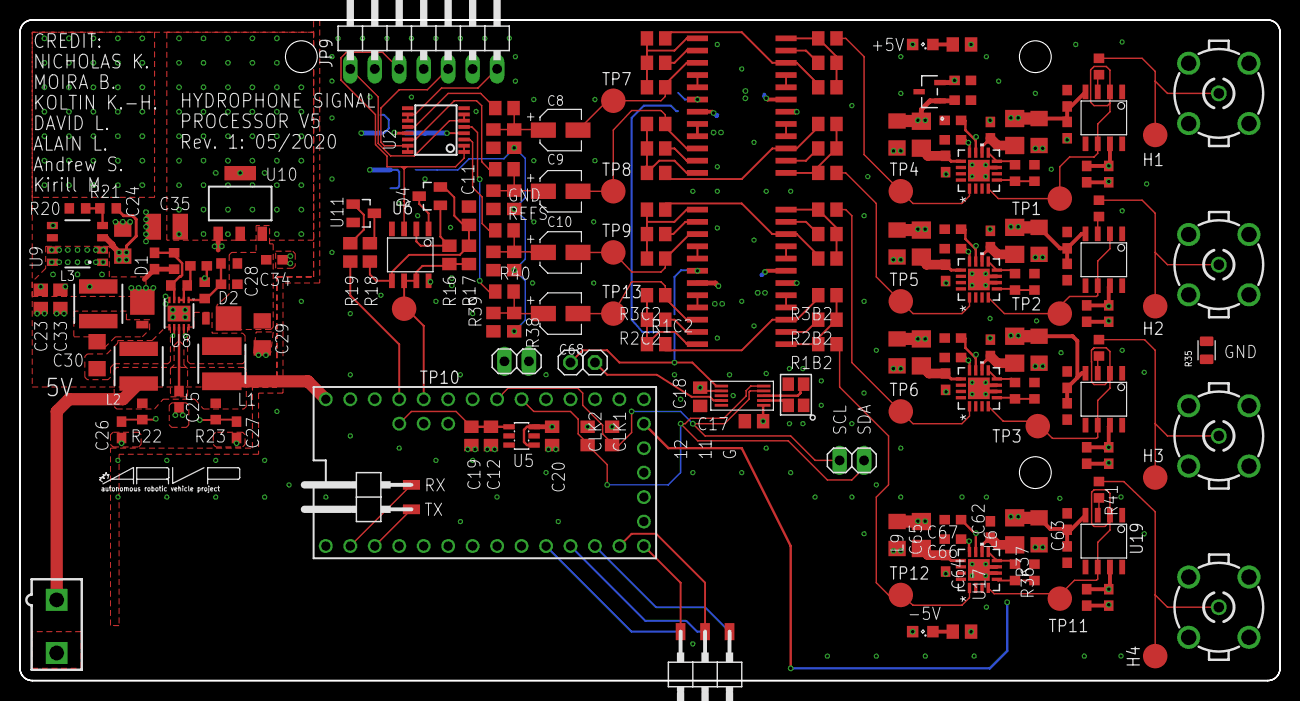
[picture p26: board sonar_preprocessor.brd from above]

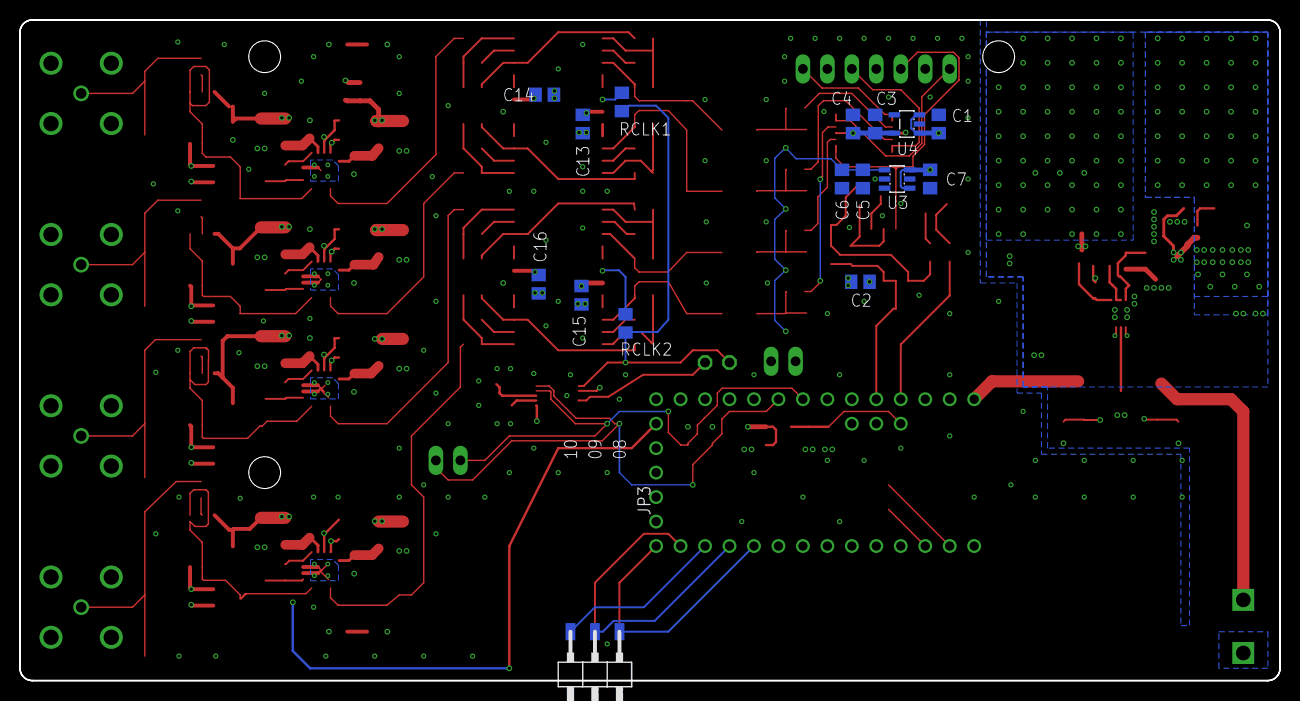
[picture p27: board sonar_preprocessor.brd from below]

Board: 4 copper layers, 130.8 x 68.6 mm, 217 parts (16 on the bottom side), 121 nets.

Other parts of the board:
U$1: A4L-LOC
U$2, U$3, U$5: STAND-OFF
U$4: ARVP

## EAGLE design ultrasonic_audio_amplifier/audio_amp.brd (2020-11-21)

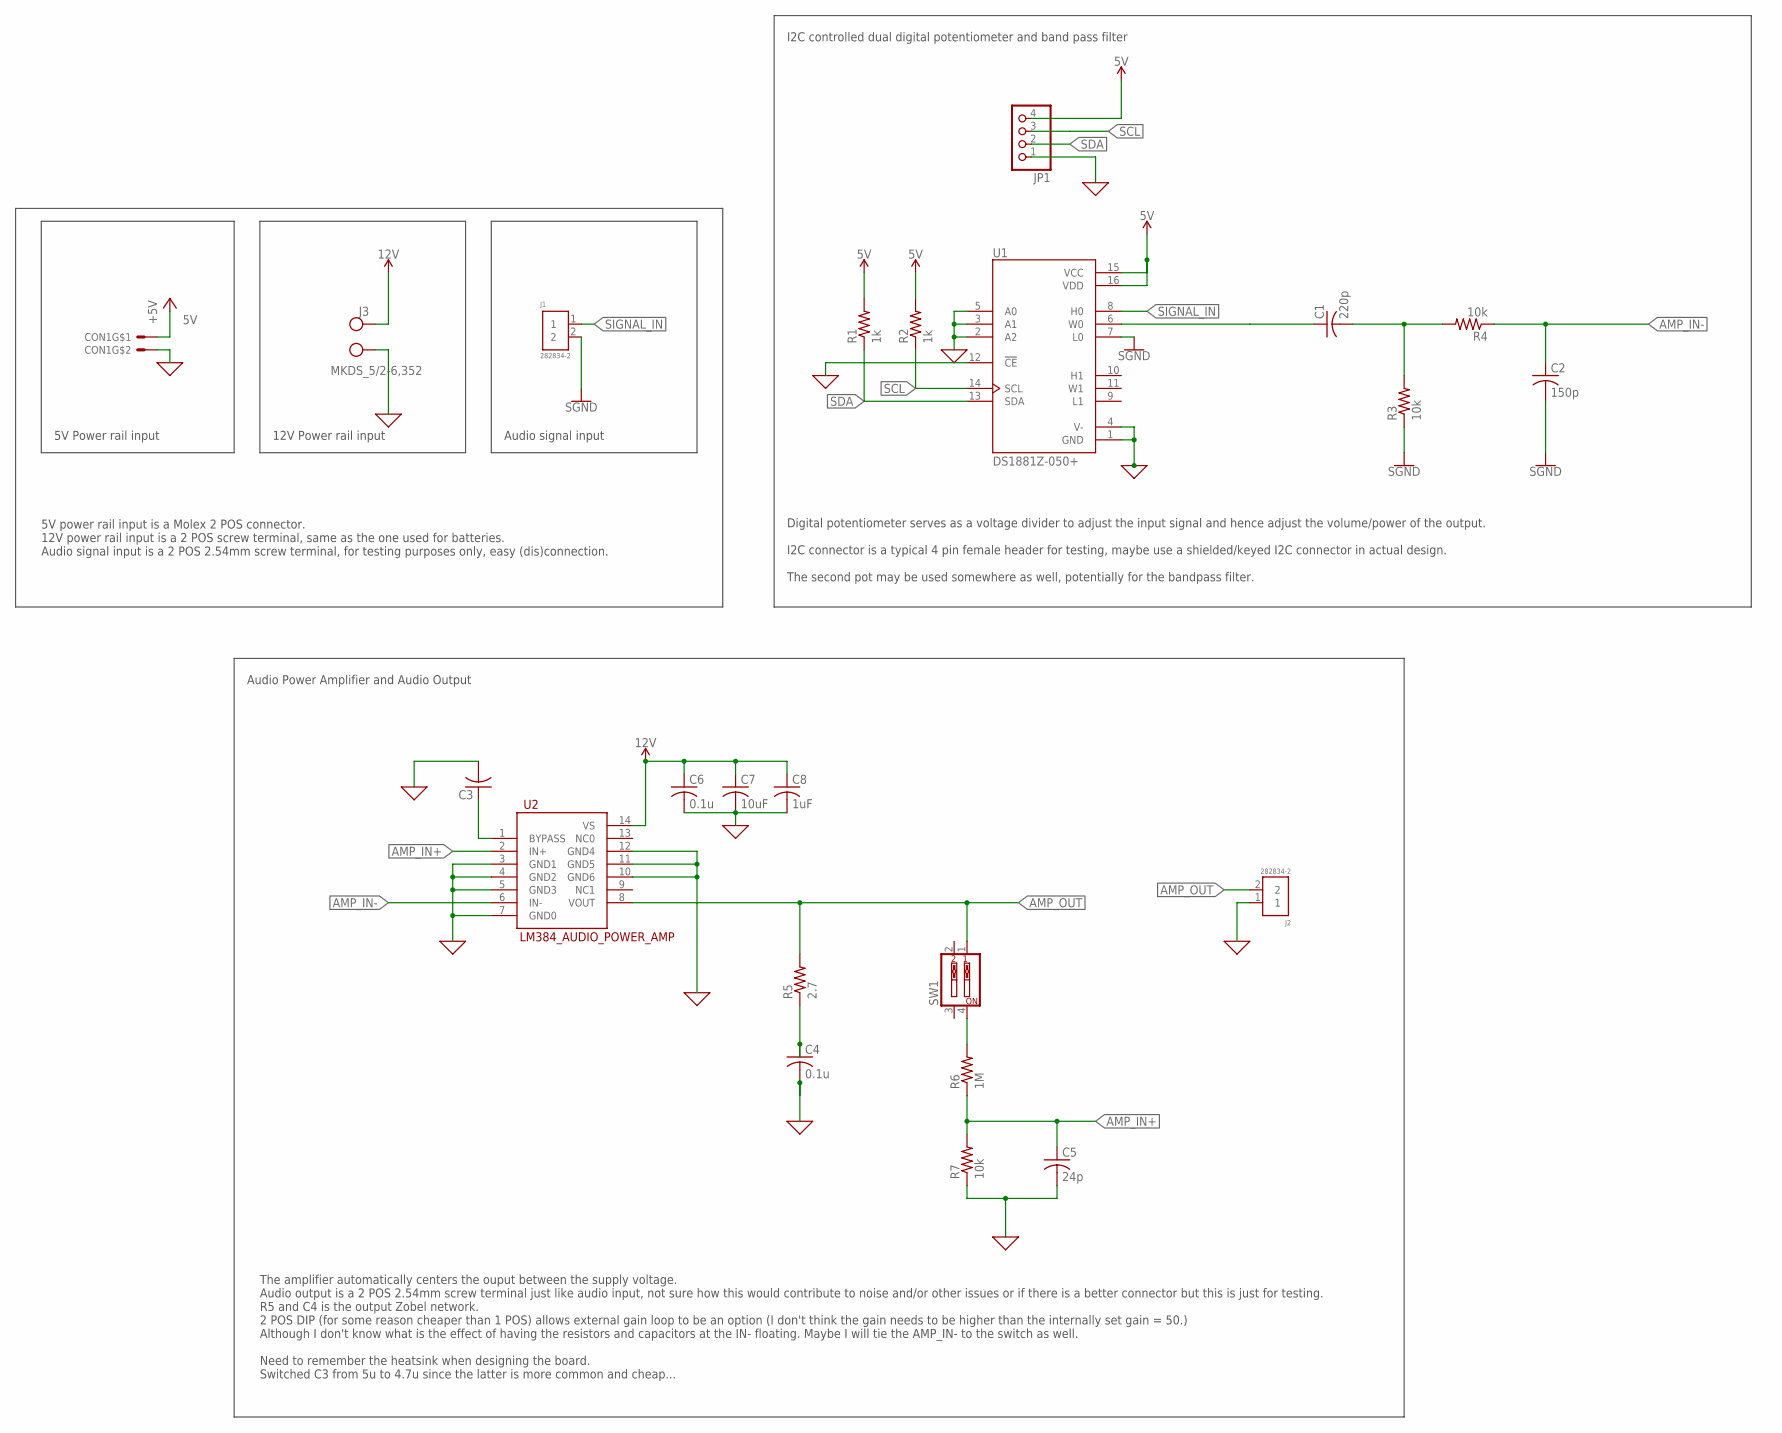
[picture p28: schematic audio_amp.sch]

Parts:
C1: 220p; CAP7.2MM*4.5MM
C2: 150p; CAP7.2MM*4.5MM
C3: C-USC0805; C0805
C4, C6: 0.1u; C0805
C5: 24p; C0805
C7: 10uF; C1206
C8: 1uF; C1206
CON1: MOLEX_5566-2; 5566-2
J1, J2: 282834-2; 2P_SCREW_TERM
J3: MKDS_5/2-6,352; MKDS_5/2-6,35
JP1: PINHD-1X4; 1X04
R1, R2: 1k; R1206
R3, R4, R7: 10k; R0805
R5: 2.7; R1206
R6: 1M; R0805
SW1: SW_DIP-2; EDG-02
U1: DS1881Z-050+; 16-SOIC
U2: LM384_AUDIO_POWER_AMP; DIP14

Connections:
0: C3.2, C4.2, C5.2, C6.2, C7.2, C8.2, CON1.2, J2.1, J3.1 (KL), JP1.1, R7.1, U1.1 (GND), U1.2 (A2), U1.3 (A1), U1.4 (V-), U1.5 (A0), U1.12 (!CE), U2.3 (GND1), U2.4 (GND2), U2.5 (GND3), U2.7 (GND0), U2.10 (GND6), U2.11 (GND5), U2.12 (GND4)
5V: CON1.1, JP1.4, R1.2, R2.2, U1.15 (VCC), U1.16 (VDD)
12V: C6.1, C7.1, C8.1, J3.2 (KL1), U2.14 (VS)
AMP_IN+: C5.1, R6.1, R7.2, U2.2 (IN+)
AMP_IN-: C2.P$1 (1), R4.1, U2.6 (IN-)
AMP_OUT: J2.2, R5.2, SW1.1, U2.8 (VOUT)
GND: C2.P$2 (2), J1.2, R3.1, U1.7 (L0)
unnamed: C1.P$2 (2), R3.2, R4.2
unnamed: C3.1, U2.1 (BYPASS)
unnamed: C4.1, R5.1
unnamed: R6.2, SW1.4
SCL: JP1.3, R2.1, U1.14 (SCL)
SDA: JP1.2, R1.1, U1.13 (SDA)
SIGNAL_IN: J1.1, U1.8 (H0)
SIGNAL_OUT: C1.P$1 (1), U1.6 (W0)

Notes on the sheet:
Audio signal input
12V Power rail input
5V Power rail input
5V power rail input is a Molex 2 POS connector. 12V power rail input is a 2 POS screw terminal, same as the one used for batteries. Audio signal input is a 2 POS 2.54mm screw terminal, for testing purposes only, easy (dis)connection.
I2C controlled dual digital potentiometer and band pass filter
Digital potentiometer serves as a voltage divider to adjust the input signal and hence adjust the volume/power of the output. I2C connector is a typical 4 pin female header for testing, maybe use a shielded/keyed I2C connector in actual design. The second pot may be used somewhere as well, potentia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
Audio Power Amplifier and Audio Output
The amplifier automatically centers the ouput between the supply voltage. Audio output is a 2 POS 2.54mm screw terminal just like audio input, not sure how this would contribute to noise and/or other issues or if there is a better connector but this is just for testing. R5 and C4 is the output Zobe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



Board: 2 copper layers, 65.0 x 30.0 mm, 23 parts (2 on the bottom side), 15 nets.

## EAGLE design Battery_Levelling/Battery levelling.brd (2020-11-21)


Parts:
3V3: LEDSMT1206; 1206
C1, C2, C3, C4: 0.01uF; C0805
C5, C6: 10u; C0805
C7: 1.5uF; C0805
C8: 10uF; C1206
CON1: MOLEX_5566-2; 5566-2
CON2, CON3: SM03B-GHS-TB
D1: DIODE-DO-214AC; DO-214AC
DANGER: LEDSMT1206; 1206
J1, J2, J3, J4, J5, J6: MKDS_5/2-6,352; MKDS_5/2-6,35
JP6: PINHD-1X2; 1X02
Q1, Q2, Q3, Q4: NMOS-TO252; TO252
Q5: DMN2011UTS; SOP65P640X120-8N
R1, R3: 220; R0805
R2, R8: 240; R1206
R4: 5.1; R1206
R5, R6, R7, R11: 100k; R1206
R9, R10: 1k; R0805
U1: TEENSY_3.1_BASIC_2
U2, U3, U4, U5: LM5050-2; MK06A
U6: IR2301S; SOIC8
U7: MCP2562-E/SN; SOIC8

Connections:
+3V3: C6.1, R8.2, U1.3.3V, U7.5 (VIO)
+5V: CON1.1, R5.2, R6.2, R7.2, R11.2
+5V1: JP6.2
AGND: U1.AGND
CANH1: CON2.P$3, CON3.P$3, U7.7 (CANH)
CANL1: CON2.P$2, CON3.P$2, U7.6 (CANL)
CANSH1: CON2.P$1, CON3.P$1
CAN_RX1: R1.2, U7.4 (RXD)
CAN_RX_T: R1.1, U1.4 (4/CAN-RX-PWM)
CAN_TX2: R3.2, U7.1 (TXD)
CAN_TX_T: R3.1, U1.3 (3/CAN-TX/PWM)
GATE1: Q1.1 (G), U2.5 (GATE)
GATE2: Q2.1 (G), U3.5 (GATE)
GATE3: Q3.1 (G), U4.5 (GATE)
GATE4: Q4.1 (G), U5.5 (GATE)
GATE5: R10.1, U6.7 (HO)
GND: 3V3.C, C1.2, C2.2, C3.2, C4.2, C5.2, C6.2, C8.2, CON1.2, CON2.P$4, CON2.P$5, CON3.P$4, CON3.P$5, DANGER.C, J1.1 (KL), J2.1 (KL), J3.1 (KL), J4.1 (KL), J5.2 (KL1), J6.1 (KL), R9.1, U1.GND, U2.2 (GND), U3.2 (GND), U4.2 (GND), U5.2 (GND), U6.3 (LIN), U6.4 (GND), U7.2 (VSS)
IO1: U1.10 (10/TX2/PWM), U6.2 (HIN)
IO2: U1.6 (6/PWM), U2.3 (OFF), U3.3 (OFF), U4.3 (OFF), U5.3 (OFF)
IO3: R5.1, U1.8 (8/TX3), U3.1 (NFGD)
IO4: R7.1, U1.5 (5/PWM), U4.1 (NFGD)
IO5: R6.1, U1.9 (9/RX2/PWM), U2.1 (NFGD)
IO6: R11.1, U1.7 (7/RX3), U5.1 (NFGD)
LEAK_IN: U1.14/A0
LED_D: R2.1, U1.23/A9 (23/A9/T/PWM)
unnamed: C8.1, J3.2 (KL1), Q5.5 (D), Q5.6 (D), Q5.7 (D), Q5.8 (D), R4.1, U6.1 (VCC)
unnamed: DANGER.A, R2.2
unnamed: D1.A, R4.2
unnamed: C7.2, U6.6 (VS)
unnamed: C7.1, D1.C, U6.8 (VB)
unnamed: Q5.4 (G), R10.2
unnamed: 3V3.A, R8.1
STB1: R9.2, U7.8 (STBY)
VBATT1: C2.1, J2.2 (KL1), Q1.3 (S), U2.4 (IN)
VBATT2: C1.1, J1.2 (KL1), Q2.3 (S), U3.4 (IN)
VBATT3: C3.1, J4.2 (KL1), Q3.3 (S), U4.4 (IN)
VBATT4: C4.1, J6.2 (KL1), Q4.3 (S), U5.4 (IN)
VIN: C5.1, U1.VIN, U7.3 (VDD)
VIN1: JP6.1
VOUT: J5.1 (KL), Q1.2 (D), Q2.2 (D), Q3.2 (D), Q4.2 (D), Q5.1 (S), Q5.2 (S), Q5.3 (S), U2.6 (OUT), U3.6 (OUT), U4.6 (OUT), U5.6 (OUT)

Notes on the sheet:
Teensy and CAN bus
5V into Teensy
Oring Config
A high side NMOS switch controls the original electronics battery (BATT0) using a high side gate driver with a bootstap circuit. When the GPIO pin is low, the NMOS is not conducting. When the GPIO pin is high, the gate driver will turn on and drive the NMOS with battery voltage+bootstrap voltage.
The LM5050MK-2 ideal diode OR control compare the voltages of the 3 motor batteries (BATT1 to BATT3) and use the one with the higher voltage to supply the electronics to achieve battery balancing. BATT0 should not be in use when the LM5050s are in use. The OFF pin on the LM5050 act like a switch, w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
The teensy controls the switching between BATT0 and BATT1-3. It also includes the CAN bus and LED signals.
IO1 is an output and controls the electronic battery BATT0. IO2 is an output and controls all the LM5050s. IO3, 4, 5 are inputs and sense the state of the NMOS on LM5050 (see if they are shorted).
The bootstrap circuit uses a capacitor C7 to store charge on a low cycle. Stored charge will be used to bias VCC to increase the voltage at HO during high cycles in order to increase the voltage between the NMOS gate and source. C7 will slowly discharge during a high cycle, so the capcitance is cho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


Board: 2 copper layers, 74.9 x 42.9 mm, 48 parts (1 on the bottom side), 36 nets.

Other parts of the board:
U$1, U$2, U$3, U$4: STAND-OFF

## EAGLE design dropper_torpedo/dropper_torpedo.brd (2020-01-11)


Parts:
C1, C2: 1u; C1206
C3, C4, C5: 10u; C0805
CON1, CON2: SM03B-GHS-TB
CON3, CON4, CON6: MOLEX_5566-2; 5566-2
D1, D2: STPS1L30A; DO214AC
JP1, JP2, JP3, JP4, JP5, JP6, JP7, JP9: PINHD-2X3; 2X03
JP8: PINHD-2X4; 2X04
JP10: PINHD-2X6; 2X06
JP11: PINHD-1X2; 1X02
LED1, LED2, LED3, LED4, LED5: LEDCHIPLED_1206; CHIPLED_1206
Q1, Q2: SI4896DY-T1-E3; SO-8
Q3, Q4: IRL6372TRPBF; SO-8
R1, R2: 3k; R1206
R3, R4, R20, R21: 10k; R1206
R5, R6: 1k; R1206
R7, R8, R25: 2k; R1206
R9, R10, R11, R12: 5k; R0805
R13: 1k; R0805
R14, R15, R16, R17: 220; EXBV8V-M
R18, R19: 220; R0805
R22, R26: 10k; EXBV8V-M
R23: 240; R1206
R24: 580; R1206
U1, U2: LTV-355T; SMD4
U3: TCAN1042HVDR; SO-8
U4: PCA9685PW; TSSOP28
U5: TEENSY_3.1_BASIC_2
X1: OSTVN05A150
X2: MOLEX_5566-4; 5566-4

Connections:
+3V3: C4.1, C5.1, JP7.1, JP7.3, JP7.5, JP9.1, JP9.3, JP9.5, JP10.1, JP10.3, JP10.5, JP10.7, JP10.9, JP10.11, R23.2, U3.5 (VIO), U4.28 (VDD), U5.3.3V
+5V: JP1.3, JP1.4, JP2.3, JP2.4, JP3.3, JP3.4, JP11.2, R24.2, X2.3
+7V: CON3.1, JP4.3, JP4.4, JP5.3, JP5.4, JP6.3, JP6.4
+12V: CON4.1, CON4.2, CON6.1, CON6.2, D1.C, D2.C, R25.2, U1.COLLECTOR (COL), U2.COLLECTOR (COL), X1.P$5, X2.2
A0: R26.6 (66), U4.1 (A0)
A0+: JP10.2, R26.3 (35)
A1: R26.5 (58), U4.2 (A1)
A1+: JP10.4, R26.4 (47)
A2: R22.8 (82), U4.3 (A2)
A2+: JP10.6, R22.1 (11)
A3: R22.7 (74), U4.4 (A3)
A3+: JP10.8, R22.2 (23)
A4: R22.6 (66), U4.5 (A4)
A4+: JP10.10, R22.3 (35)
A5: R22.5 (58), U4.24 (A5)
A5+: JP10.12, R22.4 (47)
AGND: U5.AGND
CANH: CON1.P$3, CON2.P$3, U3.7 (CANH)
CANL: CON1.P$2, CON2.P$2, U3.6 (CANL)
CANSH: CON1.P$1, CON2.P$1
CAN_RX: R19.2, U3.4 (RXD)
CAN_RX_T: R19.1, U5.4 (4/CAN-RX-PWM)
CAN_TX1: R18.2, U3.1 (TXD)
CAN_TX_T: R18.1, U5.3 (3/CAN-TX/PWM)
GND: C3.2, C4.2, C5.2, CON1.P$4, CON1.P$5, CON2.P$4, CON2.P$5, CON3.2, JP1.5, JP1.6, JP2.5, JP2.6, JP3.5, JP3.6, JP4.5, JP4.6, JP5.5, JP5.6, JP6.5, JP6.6, JP8.1, JP8.2, LED1.C, LED2.C, LED3.C, LED4.C, LED5.C, Q1.1 (S), Q1.2 (S), Q1.3 (S), Q2.1 (S), Q2.2 (S), Q2.3 (S), Q3.1 (S), Q3.3 (S), Q4.1 (S), Q4.3 (S), R1.1, R2.1, R3.1, R4.1, R13.1, R26.2 (23), U1.CATHODE (C), U2.CATHODE (C), U3.2 (GND), U4.14 (GND), U4.25 (EXTCLK), U5.GND, X2.1, X2.4
I2C_3V3: JP8.7, JP8.8, JP9.6
LED_DRAIN0: Q3.7 (D), Q3.8 (D), X1.P$4
LED_DRAIN1: Q3.5 (D), Q3.6 (D), X1.P$3
LED_DRAIN2: Q4.7 (D), Q4.8 (D), X1.P$2
LED_DRAIN3: Q4.5 (D), Q4.6 (D), X1.P$1
LED_GATE0: Q3.2 (G), R17.4 (47)
LED_GATE1: Q3.4 (G), R17.3 (35)
LED_GATE2: Q4.2 (G), R17.2 (23)
LED_GATE3: Q4.4 (G), R17.1 (11)
unnamed: LED1.A, R7.1
unnamed: LED2.A, R8.1
unnamed: LED3.A, R23.1
unnamed: LED4.A, R24.1
unnamed: LED5.A, R25.1
PCA_OE: JP7.6, R26.7 (74), U4.23 (/OE), U5.11 (11/MOSI)
PWM_CH0: R14.8 (82), U4.6 (LED0)
PWM_CH1: R14.7 (74), U4.7 (LED1)
PWM_CH2: R14.6 (66), U4.8 (LED2)
PWM_CH3: R14.5 (58), U4.9 (LED3)
PWM_CH4: R15.8 (82), U4.10 (LED4)
PWM_CH5: R15.7 (74), U4.11 (LED5)
PWM_CH6: R15.6 (66), U4.12 (LED6)
PWM_CH7: R15.5 (58), U4.13 (LED7)
PWM_CH8: R16.8 (82), U4.15 (LED8)
PWM_CH9: R16.7 (74), U4.16 (LED9)
PWM_CH10: R16.6 (66), U4.17 (LED10)
PWM_CH11: R16.5 (58), U4.18 (LED11)
PWM_CH12: R17.8 (82), U4.19 (LED12)
PWM_CH13: R17.7 (74), U4.20 (LED13)
PWM_CH14: R17.6 (66), U4.21 (LED14)
PWM_CH15: R17.5 (58), U4.22 (LED15)
PWM_SERVO0: JP4.1, R14.1 (11)
PWM_SERVO1: JP4.2, R14.2 (23)
PWM_SERVO2: JP5.1, R14.3 (35)
PWM_SERVO3: JP5.2, R14.4 (47)
PWM_SERVO4: JP6.1, R15.1 (11)
PWM_SERVO5: JP6.2, R15.2 (23)
PWM_SERVO6: JP1.1, R15.3 (35)
PWM_SERVO7: JP1.2, R15.4 (47)
PWM_SERVO8: JP2.1, R16.1 (11)
PWM_SERVO9: JP2.2, R16.2 (23)
PWM_SERVO10: JP3.1, R16.3 (35)
PWM_SERVO11: JP3.2, R16.4 (47)
RC0: C1.2, R1.2
RC1: C2.2, R2.2
SCL: JP8.5, JP8.6, R20.2, U4.26 (SCL), U5.19/A5 (19/A5/T/SCL0)
SCL_3V3: JP9.2, R20.1
SDA: JP8.3, JP8.4, R21.2, U4.27 (SDA), U5.18/A4 (18/A4/T/SDA0)
SDA_3V3: JP9.4, R21.1
STB: R13.2, U3.8 (STB)
TOPTO_A0: R9.1, R10.1, U1.ANODE (A)
TOPTO_A1: R11.1, R12.1, U2.ANODE (A)
TOPTO_E0: R5.2, R7.2, U1.EMITTER (EMIT)
TOPTO_E1: R6.2, R8.2, U2.EMITTER (EMIT)
TRP0: R10.2, U5.16/A2 (16/A2/T)
TRP0_ALT: JP7.4, R9.2
TRP1: R12.2, U5.17/A3 (17/A3/T)
TRP1_ALT: JP7.2, R11.2
TRP_GATE0: Q1.4 (G), R3.2, R5.1
TRP_GATE1: Q2.4 (G), R4.2, R6.1
TRP_RETURN0: C1.1, D1.A, Q1.5 (D), Q1.6 (D), Q1.7 (D), Q1.8 (D)
TRP_RETURN1: C2.1, D2.A, Q2.5 (D), Q2.6 (D), Q2.7 (D), Q2.8 (D)
VIN: C3.1, JP11.1, U3.3 (VCC), U5.VIN


Board: 2 copper layers, 76.2 x 50.8 mm, 72 parts (1 on the bottom side), 87 nets.

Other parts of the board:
U$5: LOGO3
U$6: LETTER_L
U$7: DOCFIELD
U$8, U$9, U$10, U$11: STAND-OFF

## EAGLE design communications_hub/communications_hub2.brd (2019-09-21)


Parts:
3V3, 5V: TPB2,54; B2,54
C1, C2, C3, C4: 10u; C0805
C5, C6: 4n7; C0805
CON1, CON2: SM04B-GHS-TB
CON3: SM02B-GHS-TB
CON6, CON7: UAVCAN_MICRO; SM04B-GHS-TB
GND: TPB2,54; B2,54
JP21: PINHD-2X20; 2X20
LED1, LED2: LEDSMT1206; 1206
P_LED1: XZDG55W-3; LED_1206
P_LED2: XZM2ACR55W-3; LED_1206
Q1, Q2: DMN5L06K; SOT23
R1, R2, R4, R5, R19, R20: 220; R0805
R9, R10, R11, R12: 10K; M1206
R13: 140; M1206
R14, R15, R16, R17: 60; R1206
R18: 85; M1206
R21: 140; R0805
R22: 66; R0805
R23: 4.7k; R0603
SJ1, SJ2: SJ
U1, U2: TCAN1042HVDR; SO-8
U$4, U$5: NUP2105L; SOT23

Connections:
+3V3: 3V3.TP, C1.1, C2.1, CON1.P$4, CON2.P$4, JP21.1, JP21.17, R9.2, R10.2, R11.1, R12.2, R22.2, R23.2, U1.5 (VIO), U2.5 (VIO)
+5V: 5V.TP, C3.1, C4.1, CON6.1 (+5V), CON7.1 (+5V), JP21.2, JP21.4, R13.2, R18.2, R21.2, U1.3 (VCC), U2.3 (VCC)
CAN0_RX_T: JP21.29, R2.1
CAN0_TX_T: JP21.31, R1.1
CAN1_RX_T: JP21.37, R5.1
CAN1_TX_T: JP21.33, R4.1
GND: C1.2, C2.2, C3.2, C4.2, C5.2, C6.2, CON1.P$1, CON1.P$5, CON1.P$6, CON2.P$1, CON2.P$5, CON2.P$6, CON3.P$3, CON3.P$4, GND.TP, JP21.6, JP21.9, JP21.14, JP21.20, JP21.25, JP21.30, JP21.34, JP21.39, LED1.C, LED2.C, Q1.2 (S), Q2.2 (S), SJ1.1, SJ2.1, U1.2 (GND), U1.8 (STB), U2.2 (GND), U2.8 (STB), U$4.3, U$5.3
GPIO_EXP_P16: JP21.22, R20.2
GPIO_EXP_P17: JP21.15, R19.2
I2C_GP0_SCL: CON2.P$3, JP21.5, R12.1
I2C_GP0_SDA: CON2.P$2, JP21.3, R10.1
I2C_GP1_SCL: CON1.P$3, JP21.28, R11.2
I2C_GP1_SDA: CON1.P$2, JP21.27, R9.1
unnamed: JP21.18, R23.1
unnamed: P_LED2.A, R13.1
unnamed: P_LED1.A, R18.1
unnamed: CON7.4 (GND), SJ1.2
unnamed: CON6.4 (GND), SJ2.2
unnamed: P_LED2.C, Q2.3 (D)
unnamed: P_LED1.C, Q1.3 (D)
unnamed: Q2.1 (G), R19.1
unnamed: Q1.1 (G), R20.1
unnamed: LED1.A, R21.1
unnamed: LED2.A, R22.1
unnamed: C5.1, R14.1, R15.2
unnamed: C6.1, R16.1, R17.2
unnamed: CON7.2 (CANH), R16.2, U2.7 (CANH), U$5.2
unnamed: CON7.3 (CANL), R17.1, U2.6 (CANL), U$5.1
unnamed: CON6.2 (CANH), R14.2, U1.7 (CANH), U$4.2
unnamed: CON6.3 (CANL), R15.1, U1.6 (CANL), U$4.1
unnamed: R1.2, U1.1 (TXD)
unnamed: R2.2, U1.4 (RXD)
unnamed: R4.2, U2.1 (TXD)
unnamed: R5.2, U2.4 (RXD)
UART1_RX: CON3.P$2, JP21.10
UART1_TX: CON3.P$1, JP21.8

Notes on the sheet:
Placed ontop of TX2 GPIO expansion headers
Expansion Header
Red LED for +5V Amber LED for +3v3 ~2V for amber, 1.3V / 20mA = 65R
Pull up resistor for GO Switch
When the Go switch is screwed all the way in, pin 18 on JP21 is pulled to GND. Under normal circumstances the Go switch will be screwed in all the way. To start the Jetson Xavier, the Go switch will have to be unscrewed, which will open circuit the path to ground and allow R23 to pull the line high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


Board: 2 copper layers, 68.0 x 33.0 mm, 46 parts (0 on the bottom side), 36 nets.

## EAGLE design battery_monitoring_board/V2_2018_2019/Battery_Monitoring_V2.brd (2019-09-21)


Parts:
ARVP1: ARVP_LOGO; ARVP
C1, C2: 0.1microF; C2012
C3, C4: 10u; C0805
CON1: MOLEX_5566-2; 5566-2
CON2, CON3: SM03B-GHS-TB
D1, D2, D3: BZT52C10; SOD-123
J1, J2, J3, J4, J5, J6, J7, J8, J9: MKDS_5/2-6,352; MKDS_5/2-6,35
JP1, JP3, JP4: PINHD-1X2; 1X02
JP2: PINHD-1X3; 1X03
JP5: PINHD-2X3; 2X03
JP6: PINHD-2X4; 2X04
Q1, Q2, Q3: TCLD1000CT; SOP-4L
Q4, Q5, Q6: PSMN1R5-30BLE; SOT404/D2PAK
Q7, Q9, Q14: SI7145DP; SO-8/PPAK/TEST; MPN SI7145DP-T1-GE3
R1, R2, R3, R18: 1k; R0805
R4, R8, R12, R13: 0.001Ohm; 3920
R5, R6, R7: 1k; M1206
R9, R10, R11: 10k; M1206
R14, R15: 10k; R1206
R16, R17: 220; R0805
R19, R20, R21: 10k; M1206; MPN RC0603FR-0710KL
U1, U2: INA3221.; HVQFN16_4X4
U3: TEENSY_3.1_BASIC_2
U4: TCAN1042HVDR; SO-8

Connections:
+3V3: C1.1, C2.1, C3.1, JP5.1, JP5.3, JP5.5, U1.4 (VS), U1.16 (VPU), U2.4 (VS), U2.5 (A0), U2.16 (VPU), U3.3.3V, U4.5 (VIO)
+5V: CON1.1, JP2.1, JP4.2, R1.1, R2.1, R3.1; also elsewhere on the board
AGND: U3.AGND
BATT1GND: D1.P$2 (A), J4.1 (KL), Q4.3S (S), R9.1, R21.1
BATT2GND: D2.P$2 (A), J3.1 (KL), Q5.3S (S), R10.1, R19.1
BATT3GND: D3.P$2 (A), J2.1 (KL), Q6.3S (S), R11.1, R20.1
BATTERY1: J1.2 (KL1); also elsewhere on the board
BATTERY2_IN: J2.2 (KL1), Q14.S@1 (S), Q14.S@2 (S), Q14.S@3 (S)
BATTERY3_IN: J3.2 (KL1), Q7.S@1 (S), Q7.S@2 (S), Q7.S@3 (S)
BATTERY4_IN: J4.2 (KL1), Q9.S@1 (S), Q9.S@2 (S), Q9.S@3 (S)
BATTERY_2: Q3.P$4 (C2), Q14.D@1 (D), Q14.D@2 (D), Q14.D@3 (D), Q14.D@4 (D), Q14.D@5 (D), R13.P$2 (2), U2.12 (IN+1)
BATTERY_3: Q2.P$4 (C2), Q7.D@1 (D), Q7.D@2 (D), Q7.D@3 (D), Q7.D@4 (D), Q7.D@5 (D), R4.P$2 (2), U1.15 (IN+2)
BATTERY_4: Q1.P$4 (C2), Q9.D@1 (D), Q9.D@2 (D), Q9.D@3 (D), Q9.D@4 (D), Q9.D@5 (D), R8.P$2 (2), U1.12 (IN+1)
CANH1: CON2.P$3, CON3.P$3, U4.7 (CANH)
CANL1: CON2.P$2, CON3.P$2, U4.6 (CANL)
CANSH1: CON2.P$1, CON3.P$1
CAN_RX1: R17.2, U4.4 (RXD)
CAN_RX_T: R17.1, U3.4 (4/CAN-RX-PWM)
CAN_TX2: R16.2, U4.1 (TXD)
CAN_TX_T: R16.1, U3.3 (3/CAN-TX/PWM)
CRITICAL_OUT: U1.9 (CRITICAL), U2.9 (CRITICAL), U3.9 (9/RX2/PWM)
E1: Q1.P$3 (E), R5.2
E2: Q2.P$3 (E), R6.2
E3: Q3.P$3 (E), R7.2
ELECTRONICS_BATTERY: R12.P$2 (2), U2.15 (IN+2); also elsewhere on the board
GND: C1.2, C2.2, C3.2, C4.2, CON1.2, CON2.P$4, CON2.P$5, CON3.P$4, CON3.P$5, J1.1 (KL), J5.2 (KL1), J6.2 (KL1), J7.2 (KL1), J8.2 (KL1), J9.1 (KL), JP1.2, JP2.3, JP6.1, JP6.2, Q4.2D (D), Q5.2D (D), Q6.2D (D), R18.1, U1.3 (GND), U1.5 (A0), U2.3 (GND), U3.GND, U4.2 (GND); also elsewhere on the board
I2C_3V1: JP5.6, JP6.7, JP6.8
MG1: D1.P$1 (C), Q4.1G (G), R5.1, R9.2
MG2: D2.P$1 (C), Q5.1G (G), R6.1, R10.2
MG3: D3.P$1 (C), Q6.1G (G), R7.1, R11.2
MOTOR1: J5.1 (KL), R8.P$1 (1), U1.11 (IN-1)
MOTOR2: J6.1 (KL), R4.P$1 (1), U1.1 (IN-3), U1.14 (IN-2)
MOTOR3: J7.1 (KL), R13.P$1 (1), U2.11 (IN-1)
unnamed: Q1.P$1 (A), R1.2
unnamed: Q2.P$1 (A), R2.2
unnamed: Q3.P$1 (A), R3.2
unnamed: JP1.1, JP3.1, Q1.P$2 (C1), Q2.P$2 (C1), Q3.P$2 (C1)
unnamed: JP2.2, JP3.2
unnamed: Q7.G, R19.2
unnamed: Q14.G, R20.2
unnamed: Q9.G, R21.2
POWER_BOARD: J8.1 (KL), R12.P$1 (1), U2.1 (IN-3), U2.14 (IN-2)
PV_OUT: U1.10 (PV), U2.10 (PV), U3.7 (7/RX3)
SCL: JP6.5, JP6.6, R14.2, U1.6 (SCL), U2.6 (SCL), U3.19/A5 (19/A5/T/SCL0)
SCL_3V1: JP5.2, R14.1
SDA: JP6.3, JP6.4, R15.2, U1.7 (SDA), U2.7 (SDA), U3.18/A4 (18/A4/T/SDA0)
SDA_3V1: JP5.4, R15.1
STB1: R18.2, U4.8 (STB)
TC_OUT: U1.13 (TC), U2.13 (TC), U3.8 (8/TX3)
VIN: C4.1, JP4.1, U3.VIN, U4.3 (VCC)
WALL: J9.2 (KL1); also elsewhere on the board
WARNING_OUT: U1.8 (WARNING), U2.8 (WARNING), U3.10 (10/TX2/PWM)

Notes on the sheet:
3.3V
Kill switch
motor GND
INA3221 MONITORING
Otoisolators
OUTPUTS
MOSFET Kill
to SDA PIN
to SCL PIN
A jumper must be used on JP3 to use the the kill switch
Kill Switch Bypass
PMOS
The wall power terminal & the electronics battery pass through the hotswap IC(sheet 2) before going to the INA then out the terminal to the power boar. This rail does not need to turn off with the kill switch and receives reverse voltage protection from the hotswap IC.
The INA3221s measure the voltage and current coming from the batteries an flowing through the sensing resistors (0.001Ohm) before leaving through the motor terminals. The sensing resistors must be connected using a Kelvin connection for the best results.
Jumpers must be used on JP4/JP5 to use the teensy & INAs
Reverse polarity protection: The source of a PMOS is connected to the battery terminal (18V); since the gate (0V) must be less than the source by at least the threshold voltage to conduct, the PMOS is always on until a negative voltage is applied.
Kill Switch: The kill switch uses darlington optioisolators and an NMOS to control the connection between the battery monitoring board GND and the motor terminal GNDs. When the magnet is in place, current is allowed to flow through the internal diode which turns on the internal BJTs of the optioiso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
UAVCAN Design Block
Motor Battery Terminals
Motor Terminals


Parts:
C5: 1n; C0805
C6, C7, C8, C9, C10: 0.1u; C0805
LED1, LED2: 2.65; SML0805
Q10, Q11, Q12, Q13: SI7145DP; SO-8/PPAK/TEST
R22, R25: 249k; R1206
R23, R26: 12.4k; R0805
R24, R27: 9.09k; R0805
R28: 158k; R0805
R29, R30: 2.32k; R0805
U5: LTC4418; 20-QFN(4X4)

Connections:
!VALID1: LED2.C, U5.!VALID1
!VALID2: LED1.C, U5.!VALID2
+5V: R29.2, R30.2; also elsewhere on the board
BATTERY1: C8.1, Q12.D@1 (D), Q12.D@2 (D), Q12.D@3 (D), Q12.D@4 (D), Q12.D@5 (D), R25.2, U5.V2; also elsewhere on the board
ELECTRONICS_BATTERY: Q11.D@1 (D), Q11.D@2 (D), Q11.D@3 (D), Q11.D@4 (D), Q11.D@5 (D), Q13.D@1 (D), Q13.D@2 (D), Q13.D@3 (D), Q13.D@4 (D), Q13.D@5 (D), U5.VOUT; also elsewhere on the board
G1: Q10.G, Q11.G, U5.G1
G2: Q12.G, Q13.G, U5.G2
GND: C5.2, C6.2, C7.2, C8.2, C9.2, C10.2, R24.1, R27.1, R28.1, U5.GND@1 (GND), U5.GND@2 (GND); also elsewhere on the board
HYS: R28.2, U5.HYS
unnamed: LED1.A, R29.1
unnamed: LED2.A, R30.1
unnamed: C5.1, U5.TMR
NIU: C6.1, U5.!SHDN, U5.EN, U5.INTVCC
OV1: R23.1, R24.2, U5.OV1
OV2: R26.1, R27.2, U5.OV2
UV1: R22.1, R23.2, U5.UV1
UV2: R25.1, R26.2, U5.UV2
VS1: C9.1, Q10.S@1 (S), Q10.S@2 (S), Q10.S@3 (S), Q11.S@1 (S), Q11.S@2 (S), Q11.S@3 (S), U5.VS1
VS2: C10.1, Q12.S@1 (S), Q12.S@2 (S), Q12.S@3 (S), Q13.S@1 (S), Q13.S@2 (S), Q13.S@3 (S), U5.VS2
WALL: C7.1, Q10.D@1 (D), Q10.D@2 (D), Q10.D@3 (D), Q10.D@4 (D), Q10.D@5 (D), R22.2, U5.V1; also elsewhere on the board

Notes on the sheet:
Bi-Directional PMOS Switch
datasheet recommend an output cap; however, due to the large capacitance on the power conversion board there is a large in-rush current that causes issues with the lab power supplies or low current sources. Therefore, the cap has been removed



Board: 2 copper layers, 57.2 x 127.0 mm, 88 parts (13 on the bottom side), 66 nets.

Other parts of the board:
U$9: LETTER_P
U$15: DOCFIELD
U$18, U$24, U$25, U$26: STAND-OFF

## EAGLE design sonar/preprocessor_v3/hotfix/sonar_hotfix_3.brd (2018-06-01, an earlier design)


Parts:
C1, C2, C3, C4, C5, C6, C7, C8, C9, C10, C11, C12: C-EUC0603; C0603
H1, H2, H3: TPB2,54; B2,54
PAD1, PAD2: WIREPADSMD5-2,5; 5-2,5
U1, U2, U3: LTC6240SO-8; SO-8
X1, X2, X3: BN35N61; B35N61
X4, X5, X6: BN35N61-HALF; B35N61-HALF

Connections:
+5V: C7.1, C8.1, C9.1, C10.1, C11.1, C12.1, PAD1.1, U1.7 (V+), U2.7 (V+), U3.7 (V+)
-5V: C1.1, C2.1, C3.1, C4.1, C5.1, C6.1, PAD2.1, U1.4 (V-), U2.4 (V-), U3.4 (V-)
GND: C1.2, C2.2, C3.2, C4.2, C5.2, C6.2, C7.2, C8.2, C9.2, C10.2, C11.2, C12.2, X1.2, X1.3 (2), X1.4 (2), X1.5 (2), X2.2, X2.3 (2), X2.4 (2), X2.5 (2), X3.2, X3.3 (2), X3.4 (2), X3.5 (2), X4.2, X4.3 (2), X5.2, X5.3 (2), X6.2, X6.3 (2)
unnamed: U1.3 (+IN), X1.1
unnamed: H3.TP, U1.2 (-IN), U1.6 (OUT), X4.1
unnamed: U2.3 (+IN), X2.1
unnamed: H2.TP, U2.2 (-IN), U2.6 (OUT), X5.1
unnamed: U3.3 (+IN), X3.1
unnamed: H1.TP, U3.2 (-IN), U3.6 (OUT), X6.1


Board: 2 copper layers, 33.0 x 50.8 mm, 26 parts (0 on the bottom side), 9 nets.

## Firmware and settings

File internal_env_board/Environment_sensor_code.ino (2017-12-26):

#include <Wire.h>
// humidity/temperature sensor
#define HIH7120ADDRESS 0x27
// pressure/temperature sensor
#define MPLADDRESS 0xC0
unsigned char buf[5];
unsigned char sta;

void setup() {
  // put your setup code here, to run once:
  Wire.begin();
  Serial.begin(115200);
  setupMPL();

}

void loop() {
  /*hum_measurement_req();
  Wire.requestFrom(HIH7120ADDRESS, 4);
  measureHIH7120();
  Serial.println(humidity());
  Serial.println(temp());*/
  delay(1000);
}
// calculates humidity from raw data
float humidity(){
   float hum = (buf[0] << 8) + buf[1];
   float humidity = float(hum)/16382*100;
   return humidity;
}
// calculates temperature from raw data
float temp(){
    float temp = (buf[2] << 6) + (buf[3] >> 2);
    float temperature = (temp/16382*165)-40;
    return temperature;
}
//must be used before to tell the HIH7120 to make a measurement
//there must be a delay between measurement request and retrieving
//the measurement from the sensor which is built into the function
//below
void hum_measurement_req(){
  Wire.beginTransmission(HIH7120ADDRESS);
  Wire.write(HIH7120ADDRESS<<1);
  Wire.endTransmission();
  delay(50);
}
// read humidity and temperature data from HIH7120
void measureHIH7120(){
  if (Wire.available()==4){
    for (int i = 0; i <4; i++){
      buf[i]=Wire.read();
    }
    if(!bitRead(buf[0], 7)&&bitRead(buf[0], 6)){
      Serial.println("Data is stale");
    }
  } else {
    Serial.print("Error in data.\n");
  }
}
// initialize Mpl sensor based on sample program from data sheet
void setupMPL(){
  Wire.beginTransmission(MPLADDRESS);
  Wire.write(0x26);
  Wire.write(0xB8);
  Wire.endTransmission();
  delay(30);
  Wire.beginTransmission(MPLADDRESS);
  Wire.write(0x13);
  Wire.write(0x07);
  Wire.endTransmission();
  delay(30);
  Wire.beginTransmission(MPLADDRESS);
  Wire.write(0x26);
  Wire.write(0xB9);
  Wire.endTransmission();
  delay(30);
}

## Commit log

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2016-12-11 Modified PCB layout, added current limiting resistor to battery voltage test pins
    [power_board.brd, power_board.sch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]
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2016-12-20 Made requested changes. When ordering be sure to tell them that I added a VSCORE layer in the middle of the board
    [AmpandADC.GBL, AmpandADC.GBO, AmpandADC.GBP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]
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2017-01-15 Version 1 of the 2017 torpedo board
    - added smoothing capacitors in parallel with the load
    - Changed the microcontroller to a teensy 3.1
    [dropper_torpedo.brd, dropper_torpedo.sch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]
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2017-02-12 Revert "Sonar breakout"
    [sonar_ampandadc.brd, sonar_ampandadc.sch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]
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2017-02-23 Updated packages for resistors and capacitors. Got rid of one unecessary capacitor
    [internal_env_board.brd, internal_env_board.sch]
2017-03-24 changed board to have HIH7120 humidity sensor, had to make custom library for the device.
    [internal_env_board.brd, internal_env_board.sch]
2017-05-16 Arduino test program for humidity sensor.
    Data is accessed correctly but sensor isn't updating data.
2017-05-16 fixed the branch
    [power_board.brd, power_board.sch, power_board_BOM.xlsx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]
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2017-05-29 Increased clearance to 7 mil
    [power_board.brd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]
2017-06-06 Fixed code. Sensor works :)
2017-06-17 Board modified to include depth sensor. Pressure sensor hasn't been tested yet.
    [internal_env_board.brd, internal_env_board.sch]
2017-06-20 changed name to better reflect board. For development of DIY SONAR amplifier plus ADC to be placed in front of Teensy
    [sonar_ampandadc.brd, sonar_ampandadc.sch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]
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2017-06-24 Routed most of the board. Missing connections to the Beaglebone
    [sonar_amp-WRONG.brd, sonar_amp-WRONG.sch, sonar_amp.brd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]
2017-06-27 Non-BNC amp board. Laid over PRUDAQ layout for reference. Need to add PWM header for servo next.
    [sonar_amp.brd, sonar_amp.sch]
2017-06-27 Added PWM, silkscreen to board. Input connection is flying lead, next iteration will have BNC inputs
    [sonar_amp.brd, sonar_amp.sch]
2017-06-27 Replaced flying lead with BNC conn. Passes APC DRU (7 mil minimums, standard drill sizes on site). Removed 1V LED (no 1V LED's on digikey)
    [sonar_amp.brd, sonar_amp.sch]
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2017-06-29 Made LMV797 GND/VCC fix (good catch Brayden). A few more aesthetic adjustments
    [sonar_amp.brd, sonar_amp.sch]
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2017-07-04 Added digital pots to I2C line. Moved servo lines. Servo 2 now overlays on top of PRUDAQ SMA header so we will need to desolder SMA header probably if we need to use servo 2
    [sonar_amp-WRONG.brd, sonar_amp-WRONG.sch, sonar_amp.brd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]
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2017-07-06 Changed terminal block layout; Modified some routing; Fixed DRC issues
    [Battery Voltage Monitoring Schematic.brd, Battery Voltage Monitoring Schematic.sch]
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2017-08-01 Fix most in SONAR issue
    [sonar_amp.brd, sonar_amp.sch]
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2017-09-26 Swapped positions of Molex connector and torpedo drivers
    [dropper_torpedo.brd, dropper_torpedo.sch]
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2017-10-08 Added LEDs; Increased clearance to 8mil
    [dropper_torpedo.brd, dropper_torpedo.sch, dropper_torpedo_BOM.xlsx]
2017-10-08 Built Schematic and PCB
    -Uses 4 open drain, very sensitive hall effects
    -The output gets fed into a 4 port NAND gate.
    -Output of NAND gate is fed through a buffer.
    -Output of HIGH means theres a magnetic field near the board.
    [killswitch.brd, killswitch.sch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]
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2017-10-08 Miss spec'ed a part
    NAND gate I choose only went up to 3.3V, I swapped it out with one
    that'll go up to 5V.
    [killswitch.brd, killswitch.sch]
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2017-10-08 Removed RJ11 and replaced with 3-pin Header
    [killswitch.brd, killswitch.sch]
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2017-10-08 pMOS in schematic wasn't attached to 5V. Fixed that.
    [killswitch.brd, killswitch.sch]
2017-10-08 Output wasnt pulling low. Using a push-pull buffer and an AND gate instead
    [killswitch.brd, killswitch.sch]
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2017-10-10 Added top layer gnd plane; Fixed MOLEX 5566 footprint
    [dropper_torpedo.brd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]
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2017-10-15 Simplified schematic
    -only need to pull low
    -removed push pull output buffer.
    -updated PCB layout
    -Need to spec the resistor value that would be in series with the common
    drain hall effects.
    [killswitch.brd, killswitch.sch]
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2017-10-29 Added BOM, Increase trace width
    -I also changed all the 0603 to 0.47uF to keep BOM simple. This actually
    increases performance at less cost and less complexity
    -All traces have been increased to 0.02 or 20mil in thickness
    [killswitch.brd, killswitch.sch, killswitch_BOM.xlsx]
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2017-11-03 Revert "Some introductory work on the led display."
    This reverts commit 024e16ed0e7cc50c5a47988cf575eef0ec900d60.
    [display_board.brd, display_board.sch, matrix.sch]
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2017-11-04 Fixed molex footprint
    [dropper_torpedo.brd, dropper_torpedo.sch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]
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2017-11-07 Fixed issue with CAM files
    [dropper_torpedo.GBL, dropper_torpedo.GBO, dropper_torpedo.GBP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]
2017-11-11 added leakage sensor connectors
    [internal_env_board.brd, internal_env_board.sch]
2017-11-13 Schematic with suggestions made by Alain implemented.
    I've implemented the suggestions from the last meeting, and I will begin work on the PCB once it is reviewed.
    [powerboard_monitor.sch]
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2017-11-14 Fixed issue with i2c net labeling
    [dropper_torpedo.GBL, dropper_torpedo.GBO, dropper_torpedo.GBP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]
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2017-11-18 Fixed GND's and removed AGND's
    [Battery_Monitoring_with_kill_Schematic.sch]
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2017-11-18 Schematic - 3
    Fixed the issue as pointed out on Freedcamp by Alain
    [powerboard_monitor.sch]
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2017-11-22 changed dimensions and fixed layer text
    [internal_env_board.brd, internal_env_board.sch]
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2017-11-25 Swapped old MPL3115 footprint with new one
    [internal_env_board.brd, internal_env_board.sch]
2017-11-25 Fixed clearance issue in HIH7120 footprint
    [internal_env_board.brd, internal_env_board.sch]
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2017-11-25 Board (v.3)
    -Various traces made wider (5V, Digital outputs)
    -Fixed the dimensions of the board.
    Note: The board meets the design rules as uploaded by Alain on 11-24-2017
    [powerboard_monitor.brd]
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2017-11-25 Board (v.4)
    Fixed the issue of islanding.
    [powerboard_monitor.brd]
2017-11-25 Board (v.5)
    Added vias from top plane to bottom plane.
    Flipped the capacitor so it is closer to VS pin.
    [powerboard_monitor.brd]
2017-11-25 Added jumpers to schematic and finished the PCB. The PCB has not been checked with the new DRC.
    [Battery_Monitoring_with_kill_Schematic.brd, Battery_Monitoring_with_kill_Schematic.sch]
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2017-11-27 Rerouted the motor and battery lines to the INA's. Changed the MOSFET drain routes.
    [Battery_Monitoring_with_kill_Schematic.brd]
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2017-11-29 Fixes as asked for in pull request
    [Bill of Materials.xlsx, powerboard_monitor.brd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]
2017-11-29 Changed CAN bus connector back to JST GH series due to long Digikey lead time for PH crimp connectors
    [dropper_torpedo.GBL, dropper_torpedo.GBO, dropper_torpedo.GBP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]
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2017-12-01 minor fixes, cant find jst-gh part
    [internal_env_board.brd, internal_env_board.sch]
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2017-12-01 new conn for can bus and leak sensors, new routes
    [internal_env_board.brd, internal_env_board.sch]
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2017-12-02 Finished first revision of communication hub board. Needs to be reviewed before commit.
    [i2c_board.brd, i2c_board.sch]
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2017-12-03 Fixed issue where motors could still find ground return path even when battery was disconnected by mosfet
    [Battery_Monitoring_with_kill.GBL, Battery_Monitoring_with_kill.GBO, Battery_Monitoring_with_kill.GBP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]
2017-12-03 Added 5V pin to CAN connectors in case ESC CAN transceivers require external 5V
    [communication-hub.brd, communication-hub.sch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]
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2017-12-05 Corrected 2x3 header qty in BOM
    [internal_env_board_BOM.xlsx]
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2017-12-06 Edited the BOM, cleaned up some errors.
    [Teensy_CommBus_BOM.xlsx, partlist.csv]
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2017-12-07 Fixed qty of 1x2 headers
    [CommBus_BOM.xlsx]
2017-12-08 Fixed qty 240 ohm res
    [internal_env_board_BOM.xlsx]
2017-12-08 Fixed qty JST 2 pin conn
    [internal_env_board_BOM.xlsx]
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2018-01-16 Swapped out Zener Diode
    [sonar_amp.brd, sonar_amp.sch]
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2018-01-28 Finished PCB: Implemented Alain suggestions. Properly terminated unused op amps and added in the new 100MHz OPA2354AIDGKR op amps
    [sonar_amp.brd, sonar_amp.sch]
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2018-02-04 First Revision
    First Revision of the variable gain amplifier for the sonar board. Designed for testing.
    [Sonar-Amplifier.brd, Sonar-Amplifier.sch]
2018-02-04 Revert "Merge branch 'amplifier' into sonar_preprocessor_v3"
    This reverts commit 540102cfd5a4b1681464287940d3c6b068a53623, reversing
    changes made to de64d5886ef795e5a61c97630054a831d31d3a9c.
    [Sonar-Amplifier.brd, Sonar-Amplifier.sch]
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2018-02-05 re-upload after failed merge
    [Sonar-Amplifier.brd, Sonar-Amplifier.sch]
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2018-02-13 Complted bom, made a couple package changes on schematic to conver them to 0805
    [sonar_amp.brd, sonar_amp.sch, sonar_amp_BOM..xlsx]
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2018-03-10 Replaced beaglebone footprint with some pinheaders
    [sonar_preprocessor.brd]
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2018-03-21 Reworked board dimensions and mounting
    [sonar_preprocessor.brd, sonar_preprocessor.sch]
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2018-03-29 Added the design block
    All components on the top layer. Made footprint as small as possible.
    Area is less than 15.30 x 10.9 mm
    [Amplifier-Sonar-Prototype-BOM.xlsx, Sonar-Amplifier-Prototype.brd, Sonar-Amplifier-Prototype.sch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]
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2018-03-30 Added a little bit more clearance
    [Sonar-Amplifier.brd]
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2018-03-31 placed bypass caps and Rclk on bottom of board. Renamed BOM.xlsx to BOM_prototype.xlsx
    [BOM_prototype.xlsx, filter.brd]
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2018-04-03 GND fixed
    [Sonar_Power_Schematic.brd, Sonar_Power_Schematic.sch, Sonar_Power_Schematic_LT1117.brd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]
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2018-04-13 reworked filter and clock routing
    [sonar_preprocessor.brd, sonar_preprocessor.sch]
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2018-04-15 fixed f/b annotation breaking issue; Added LEDs to +-5V rails
    [sonar_preprocessor.brd, sonar_preprocessor.sch]
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2018-05-19 Added and move GND wire pads and added a top and bootom GND plane
    [Power_Monitoring_Schematic.brd, Power_Monitoring_Schematic.sch]
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2018-09-15 Added TVS diodes. Needs some work.
    Passes most DRC but has a few airwires.
    [communication-hub.brd, communication-hub.sch]
2018-09-15 Turns out those airwires aren't an issue.
    [communication-hub.brd]
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2018-11-07 Finally got around to finishing this.
    Added test points and power bus indication LEDs.
    [communication-hub.brd, communication-hub.sch]
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2018-11-17 Completed error-checking, generated CAM
    [LeakSensor.brd, LeakSensor.sch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]
2018-11-17 Fixed issues.
    [communication-hub.brd]
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2018-11-25 Revert "Merge branch 'develop' into communications_hub-tvs-david"
    This reverts commit ab89ead97715090ee32798ddfa3cee6332a63a0d, reversing
    changes made to a250170e917bb120169c4520e22500f14d1f000b.
    [Amplifier-Sonar-Prototype-BOM.xlsx, BOM_prototype.xlsx, Power_Monitor_BOM.xlsx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]
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2018-12-01 Regenerated CAM data and re-ran error-check
    [LeakSensor.brd, LeakSensor.sch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]
2018-12-09 Added LCD parts to BOM and fixed silkscreen
    [internal_env_board_with_LCD.brd, internal_env_board_with_LCD.sch]
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2018-12-12 Fixed some polygons
    [sonar_preprocessor.brd]
2018-12-14 Added parts to BOM
    - 140 & 68ohm resistors for LEDs
    - NUP2105L for CAN bus protection
    - Replaced old TCAN1042 chip with MCP2562 (chip we are currently using)
    [Teensy_CommBus_BOM.xlsx]
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2018-12-22 Revert "Added new components for LCD"
    This reverts commit b3b33264bb3048065967870ae9c2541e4a61a1bf.
    [internal_env_board_with_LCD.brd, internal_env_board_with_LCD.sch]
2018-12-22 Revert "Revert "Added new components for LCD""
    This reverts commit c0bbbe6875a79572ef2507bb7a73dc54051defa6.
    [internal_env_board_with_LCD.brd, internal_env_board_with_LCD.sch]
2018-12-22 Revert "Added new components for LCD on board"
    This reverts commit 525a6551a790c18222fb1f502ed1c1a08163eb89.
    [internal_env_board_with_LCD.brd, internal_env_board_with_LCD.sch]
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2018-12-26 JLCPCB didn't like where my origin was so I moved it :P
    [copper_bottom_l4.gbr, copper_inner_l2.gbr, copper_inner_l3.gbr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]
2019-01-26 Fixed a typo
    [communication-hub.brd, communication-hub.sch]
2019-01-26 Fixed BOM :(
    [Teensy_CommBus_BOM.xlsx]
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2019-03-11 fixed schematic errors, PCB in progress
    [Battery_Monitoring_V2.brd, Battery_Monitoring_V2.sch]
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2019-04-21 I should really be studying for finals.
    Final tweaks to schematic.
    I can't find anything terrible about either the layout or the schematic,
    but I'm certain there's something wrong.
    [integrated_adc.sch]
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2019-05-02 Implemented fixes/changes.
    The issues were discussed on April 30, 2019
    [integrated_adc.brd, integrated_adc.sch]
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2019-05-11 Fixed silkscreen, added new pdf for the board
    [Battery_Monitoring_V2.brd, Battery_Monitoring_V2.sch]
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2019-05-11 Added in preprocessor_v3 which I had mistakenly removed in a previous commit.
    [Amplifier-Sonar-Prototype-BOM.xlsx, BOM_prototype.xlsx, Sonar-Amplifier-Prototype.brd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]
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2019-05-18 Jumpers are removed, connectors to TCAN are replaced, CON4 and CON5 are removed.
    [communications_hub2.brd, communications_hub2.sch]
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2019-05-26 Fixed wire stubs, updated BOM
    [Battery_Monitoring_V2.brd, Battery_Monitoring_V2_BOM.xlsx]
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2019-06-08 Add files via upload
    Updated BOM to remove wrong temperature sensor connector that is unnecessary for this board.
    [internal_env_board_with_LCD_BOM .xlsx]
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2019-06-19 com hub fix, R3/R6/R7/R8 removed and STBY pins pulled to GND
    [BOM.xlsx, communications_hub2.brd, communications_hub2.sch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]
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2019-09-21 Moved current comm hub into correct place, deleted old versions
    [BOM.xlsx, Communication.sch, Teensy_CommBus_BOM.xlsx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]
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2021-07-23 Fixing trace width.
    [actuator.brd]
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2021-10-16 Routed some airwires, removed fixed network resistor.
    [actuator.brd, actuator.sch]
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

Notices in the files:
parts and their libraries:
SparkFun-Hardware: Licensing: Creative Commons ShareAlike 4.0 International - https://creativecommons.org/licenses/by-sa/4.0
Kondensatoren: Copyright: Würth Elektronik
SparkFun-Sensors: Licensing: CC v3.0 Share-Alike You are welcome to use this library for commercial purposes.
